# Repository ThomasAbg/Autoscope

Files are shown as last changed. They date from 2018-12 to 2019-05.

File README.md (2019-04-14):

# Autoscope - Latex template

## Dependencies

```
sudo apt-get install texlive-full python-pygments python-pip
sudo pip install pygments-style-monokailight
```

<br>

## Build

```
xelatex --shell-escape main.tex
```

<br>

## Provided commands

### Include code

Include a source code block :
```latex
\code{c}
void main(void){
    /*C code example*/
    }
\end{minted}
```

Include code in line :
```latex
\codeinline{text}{/*formatted text*/}
```

### Include figures

Set path to figures in `main.tex` :
```latex
\newcommand{\figures}{path/to/figures}
```

Include a figure :
```latex
\begin{figure}[H]
    \centering
    \includegraphics[width=0.3\linewidth]{\figures/image.png}
    \decoRule
    \caption[
    <Subtitle>]{
    <Subtitle>}
    \label{fig:<Subtitle>}
    \end{figure}
```

### Include equations

- `&` : Align columns
- `\\` : New ligne
- `^{}` : Superscript
- `_{}` : Subscript
- `\frac{}` : Fraction
- `\left(` & `\right)` : Scaled parenthesis
- `\left[` & `\right]` : Scaled braces

Example :
```latex
\begin{align*}
p(r,\theta,\varphi)&=G(\theta,\varphi)\cdot\left(\frac{P_{in}}{4\pi\cdot r^{2}}\right)&&(W/m^{2})\\
&=D(\theta,\varphi)\cdot\frac{P_{out}}{4\pi\cdot r^{2}}
\end{align*}
```

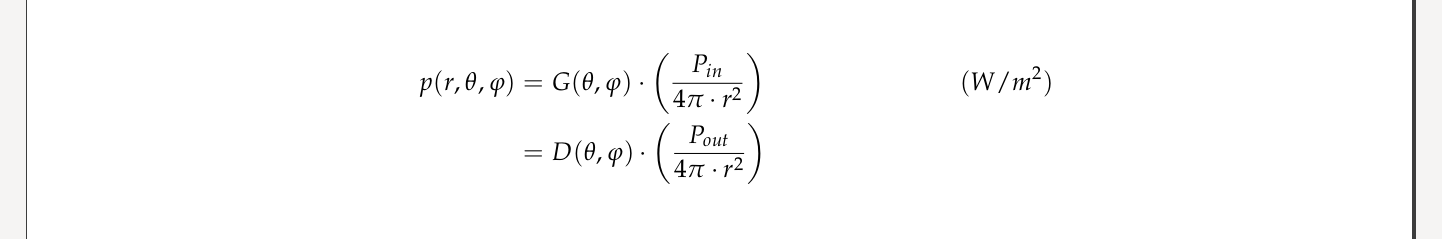
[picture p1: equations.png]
example_equations


### Include lists

Use `[label=$\bullet$]` for first level :
```latex
\begin{itemize}[label=$\bullet$]
	\item <item1>
	\item <item2>
	\item \begin{itemize}
		\item <item3.1>
		\item <item3.2>
		\end{itemize}
	\end{itemize}
```

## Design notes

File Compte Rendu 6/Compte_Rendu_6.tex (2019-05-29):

%.$ xelatex --shell-escape TP1.tex

%path to figures
\newcommand{\figures}{./Figures}

\documentclass[
11pt,
oneside,
french,
singlespacing,
liststotoc,
toctotoc,
headsepline,
]{MastersDoctoralThesis}

\usepackage{mathpazo}
\usepackage{fontspec}
\setmainfont[Ligatures=TeX, Mapping=tex-text]{TeX Gyre Pagella}
\setmonofont{FreeMonoBold}
\usepackage[backend=bibtex, style=authoryear, natbib=true]{biblatex}
\addbibresource{example.bib}
\usepackage[autostyle=true]{csquotes}
\usepackage{enumitem}
\usepackage{float}
\usepackage{amsmath}
\usepackage{minted}
\usepackage{xcolor}

\geometry{
	paper=a4paper,
	inner=2.5cm,
	outer=2.5cm,
	bindingoffset=0.5cm,
	top=1.5cm,
	bottom=1.5cm,
	}

\thesistitle{Autoscope\\Compte rendu final}
\supervisor {}
\examiner{}
\degree{\href{http://www.estei.fr/filiere/informatique-systemes-embarques}{MASTER Systèmes Embarqués}}
\author{Thomas ABGRALL\\Clément AILLOUD\\Thibaud LE DOLEDEC\\\href{https://www.github.com/thomaslepoix}{Thomas LEPOIX}}
\addresses{}
\subject{}
\keywords{}
\university{\href{http://www.estei.fr}{E.S.T.E.I.}}
\department{\href{http://www.estei.fr}{École Supérieure des Technologies Électronique, Informatique, et Infographie}}
\group{\href{http://www.estei.fr/filiere/informatique-systemes-embarques}{Département Systèmes Embarqués}}
\faculty{\href{http://www.estei.fr}{E.S.T.E.I.}}

\AtBeginDocument{
	\hypersetup{pdftitle=\ttitle}
	\hypersetup{pdfauthor=\authorname}
	\hypersetup{pdfkeywords=\keywordnames}
	}

\begin{document}

\mainmatter
\pagestyle{plain}
\usemintedstyle{monokailight}
%bash/Ruby/basemake/
\definecolor{gris}{gray}{0.97}
\definecolor{gris2}{HTML}{282828}
\definecolor{ubuntu}{HTML}{300A24}

\newcommand{\code}[1]{\begin{minted}[
linenos,
breaklines,
breakautoindent,
breakaftersymbolpost,
bgcolor=gris,
fontsize=\scriptsize,
obeytabs,
tabsize=4,
showtabs,
]{#1}}

\newcommand{\codeinline}[2]{\mintinline[fontsize=\footnotesize]{#1}{#2}}

%------------------------------------------------------------------

\begin{titlepage}
\begin{center}

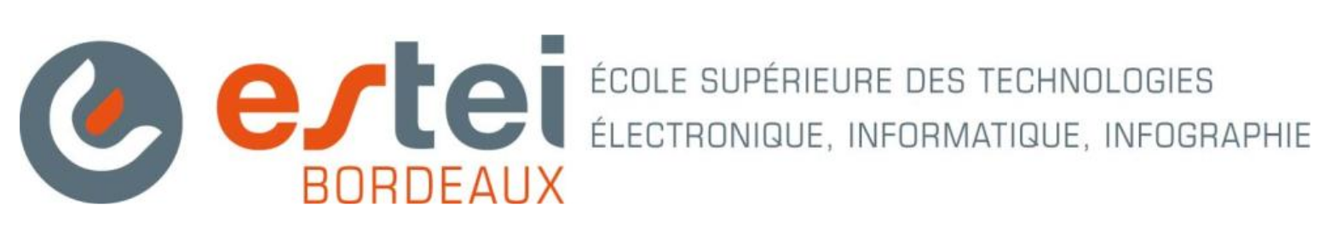
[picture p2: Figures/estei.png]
{\href{http://www.estei.fr}{}}
\vspace*{.06\textheight}
\vspace{1.5cm}\\
\textsc{\Large Projet de MASTER 2}\\[0.5cm]

\HRule \\[0.4cm]
{\huge \bfseries \ttitle\par}\vspace{0.4cm}
\HRule \\[1.5cm]

\large{\emph{Auteurs :}\\
\authorname}

\vspace{4cm}
\degreename\\[1cm]
{\vspace{0.4cm}\scshape\LARGE \univname}\\\deptname\\\groupname\\[1cm]

\vfill

{\large \today}\\[1cm]

\end{center}
\end{titlepage}

%------------------------------------------------------------------

%\begin{acknowledgements}
%\addchaptertocentry{\acknowledgementname} % Add the acknowledgements to the table of contents
%\end{acknowledgements}

\tableofcontents

\pagestyle{thesis}

%chapter Cahier des charges
%chapter Structure 3D
%chapter Hardware
%chapter Middleware
%chapter Software
%chapter Conclusion

\part{Partie de groupe}
\include{Chapters/Chapter1}
\include{Chapters/Chapter2}
\include{Chapters/Chapter3}
\include{Chapters/Chapter4}
\include{Chapters/Chapter5}
\include{Chapters/Chapter6}
\include{Chapters/Chapter7}
\part{Thomas LEPOIX}
%\include{Chapters/Lepoix/Chapter1}
\include{Chapters/Lepoix/Chapter2}
\include{Chapters/Lepoix/Chapter3}
\include{Chapters/Lepoix/Chapter4}
\include{Chapters/Lepoix/Chapter5}
\part{Thomas ABGRALL}
\include{Chapters/Abgrall/Chapter1}
\include{Chapters/Abgrall/Chapter2}
%\include{Chapters/Abgrall/Chapter3}
%\part{Clément AILLOUD}
%\include{Chapters/Ailloud/Chapter1}

\appendix

%\include{Appendices/AppendixA}

\end{document}

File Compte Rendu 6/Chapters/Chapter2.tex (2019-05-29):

\chapter{Optique}

\section{Explications sur le télescope de Dobson}

Le télescope est un instrument permettant d'observer le ciel en amplifiant la lumière captée des astres et en agrandissant l'image vue. Il réalise cela par un jeu de miroirs, à la différence de la lunette astronomique qui utilise un jeu de lentilles.

Il existe plusieurs types de télescope, celui de Newton est composé d'un miroir parabolique "primaire" concentrant la lumière vers un miroir plan "secondaire" la déviant vers l'oculaire, où l'utilisateur place son œil.

\begin{figure}[H]
    \centering
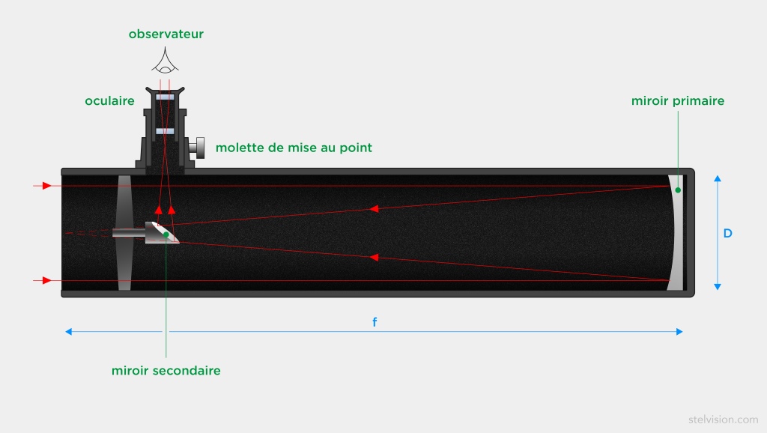
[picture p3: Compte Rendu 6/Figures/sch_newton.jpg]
    
    \decoRule
    \caption[
    Schéma du télescope de Newton\\(Schéma \textcopyright Stelvision)]{
    Schéma du télescope de Newton\\(Schéma \textcopyright Stelvision)}
    \label{fig:Schéma du télescope de Newton (Schéma copyright Stelvision)}
    \end{figure}

\vspace{1cm}

L'amplification lumineuse dépend du diamètre $D$ du miroir parabolique. Le grossissement dépend de la distance focale de la parabole $f$. Le diamètre détermine la luminosité et la finesse de l'image. La distance focale détermine le grossissement. Trop agrandir l'image par augmentation de la distance focale assombrit et dégrade sa qualité.

\vspace{1cm}

Le télescope de Dobson est un télescope de Newton doté d'une monture azimutale simplifiée. Il a été inventé par un astronome amateur et a les avantages d'être simple de fabrication et relativement peu onéreux pour un télescope.

\begin{figure}[H]
    \centering
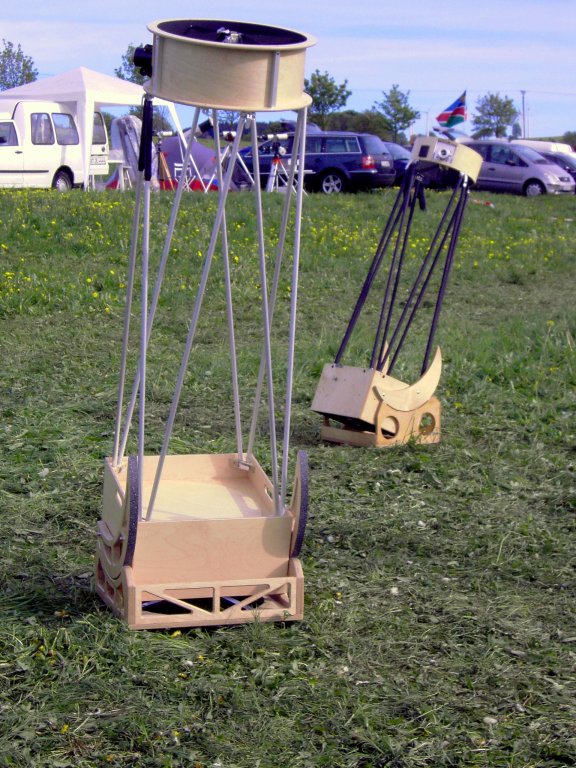
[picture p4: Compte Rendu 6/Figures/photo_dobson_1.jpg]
    
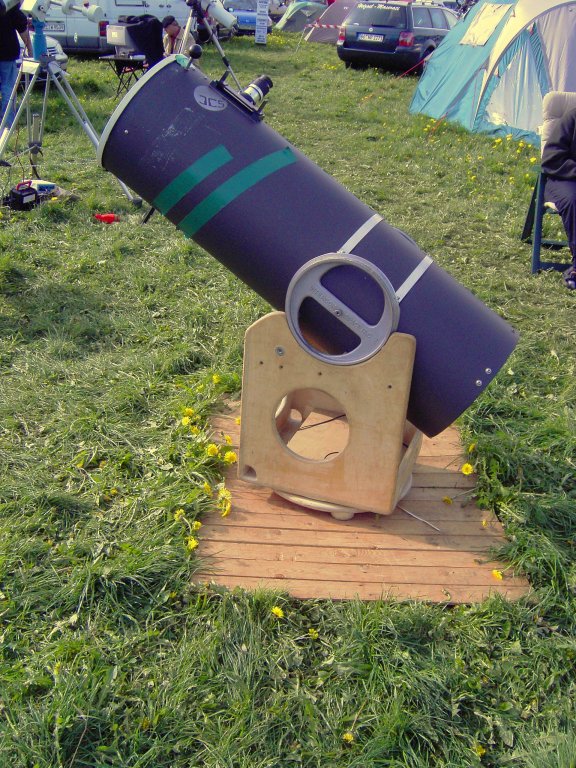
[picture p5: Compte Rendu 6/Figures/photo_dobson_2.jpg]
    
    \decoRule
    \caption[
    Télescopes de Dobson]{
    Télescopes de Dobson}
    \label{fig:Télescopes de Dobson}
    \end{figure}

\section{Choix de l'oculaire}

L'oculaire d'un télescope est un jeu de lentilles placé au plan focal de l'image produite par celui-ci. Il sert avant tout à faire de cette image présente au plan focal une image "à l'infini", c'est-à-dire nette sans accommodation de l'œil. Il permet également, par sa propre distance focale, d'ajuster le grossissement du télescope.

\begin{align*}
G&=\frac{f_{miroir primaire}}{f_{oculaire}}
\end{align*}

\vspace{1cm}

Un zoom est un objectif à lentilles mobiles et à distance focale variable. Il permet donc d'ajuster l'angle d'ouverture de l'appareil et de modifier son grossissement. Il existe des oculaires zoom pour télescope.

\vspace{1cm}

Le site internet Stelvision met à disposition un simulateur d'oculaires. Il permet, pour un télescope de caractéristiques $f$ et $D$ données, de visualiser l'image produite avec des oculaires de distances focales différentes. Quelques astres sont observables.

{\href{https://www.stelvision.com/simulateur-telescope/simulateur-telescope.php}{\codeinline{text}{https://www.stelvision.com/simulateur-telescope/simulateur-telescope.php}}}

\vspace{1cm}

Les caractéristiques de l'Autoscope sont les suivantes~:

\begin{align*}
D&=254mm&f&=1,27m
\end{align*}

\begin{figure}[H]
    \centering
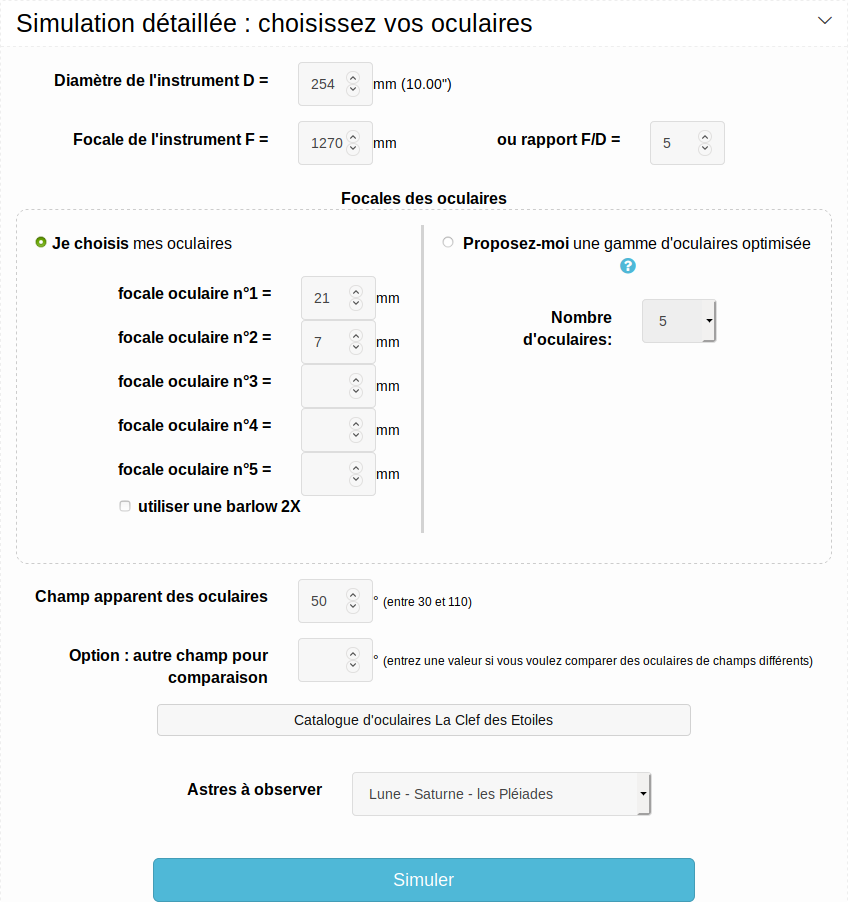
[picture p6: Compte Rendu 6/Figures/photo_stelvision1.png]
    
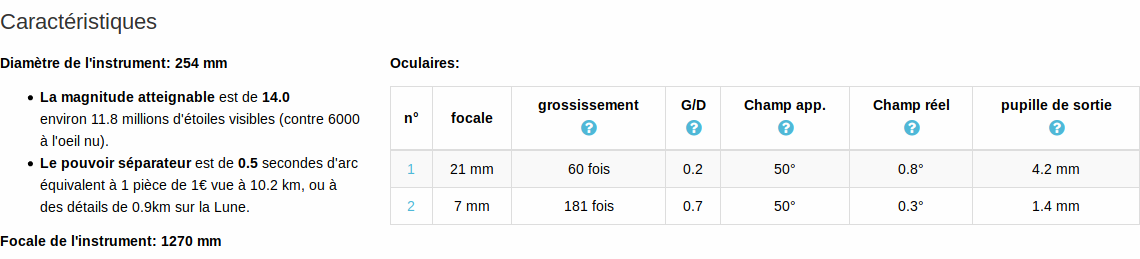
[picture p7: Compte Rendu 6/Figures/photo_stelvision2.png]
    
    \decoRule
    \caption[
	Simulateur de télescope Stelvision.com]{
    Simulateur de télescope Stelvision.com}
    \label{fig:Simulateur de télescope Stelvision.com}
    \end{figure}

\begin{figure}[H]
    \centering
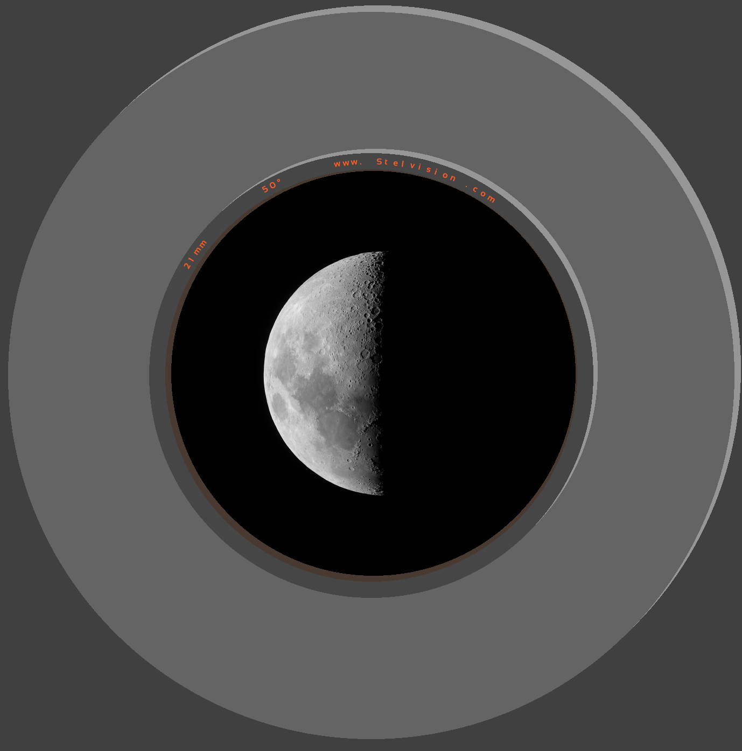
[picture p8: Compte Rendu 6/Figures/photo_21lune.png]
    
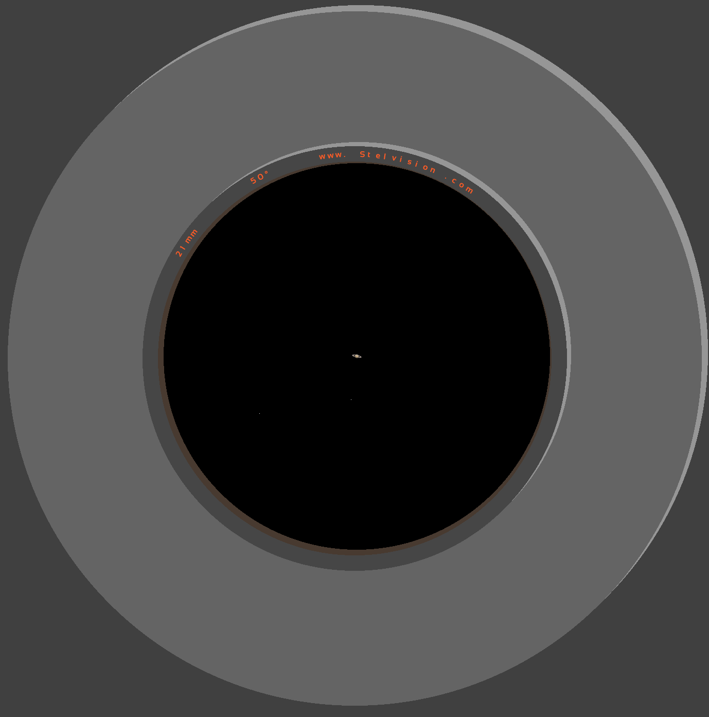
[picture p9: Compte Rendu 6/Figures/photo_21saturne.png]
    
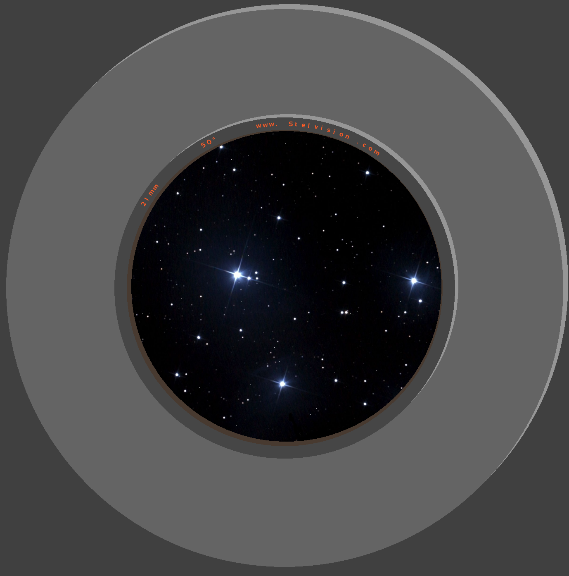
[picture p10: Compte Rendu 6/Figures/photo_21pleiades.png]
    
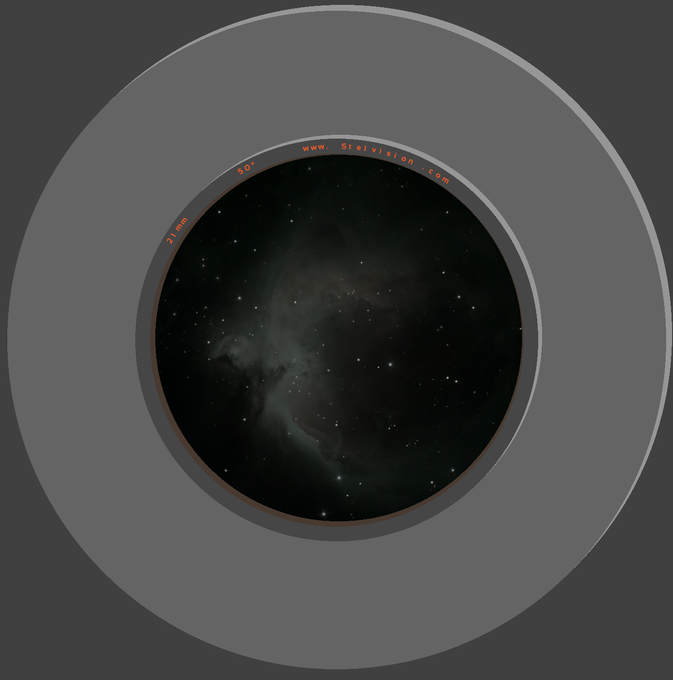
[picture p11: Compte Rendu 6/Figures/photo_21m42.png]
    
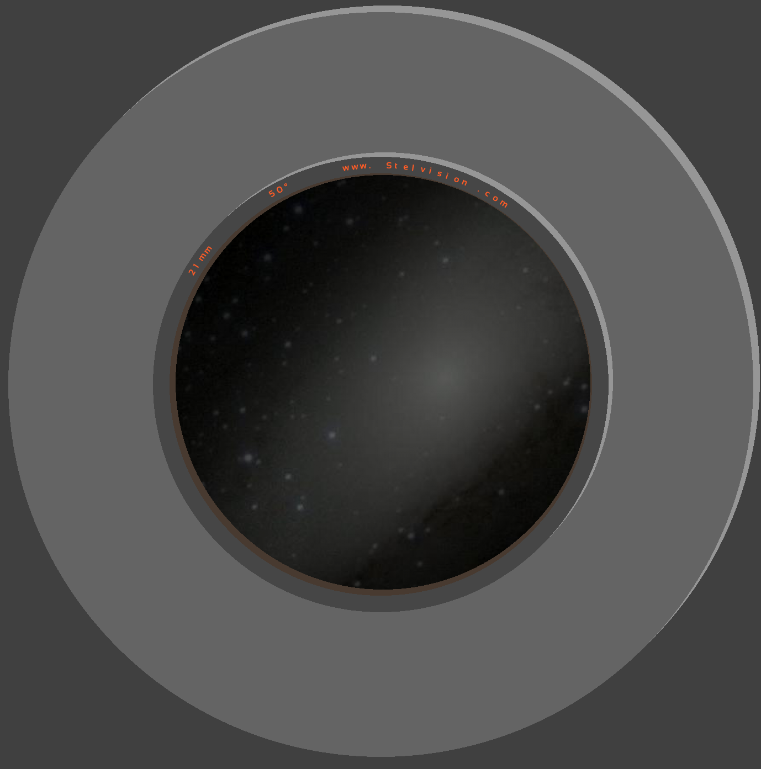
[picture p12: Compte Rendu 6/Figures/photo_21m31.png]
    
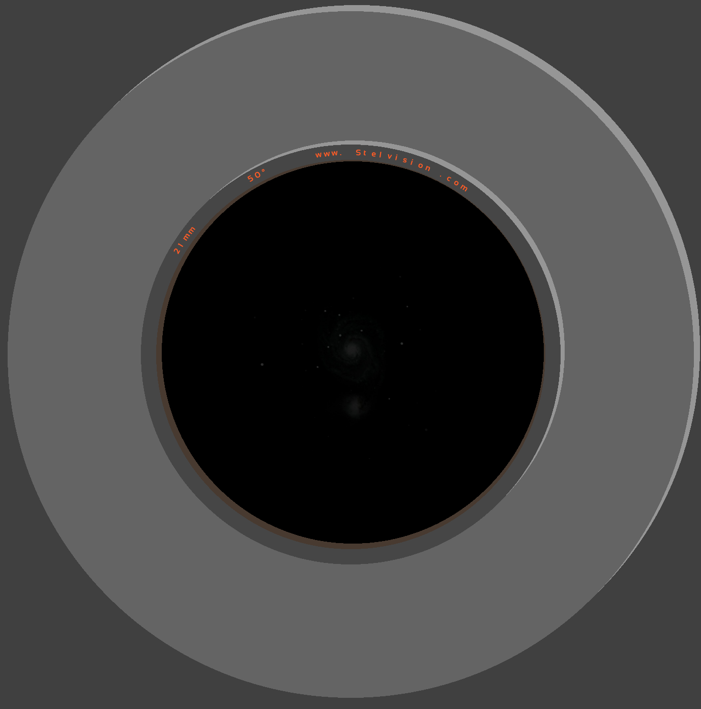
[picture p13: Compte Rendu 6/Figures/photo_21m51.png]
    
    \decoRule
    \caption[
	Résultats de simulation pour un oculaire de focale $f=21mm$\\Lune, Saturne, les Pléiades,\\galaxies M42, M31, M51]{
	Résultats de simulation pour un oculaire de focale $f=21mm$\\Lune, Saturne, les Pléiades,\\galaxies M42, M31, M51}
    \label{fig:	Résultats de simulation pour un oculaire de focale $f=21mm$ Lune, Saturne, les Pléiades, galaxies M42, M31, M51}
    \end{figure}

\begin{figure}[H]
    \centering
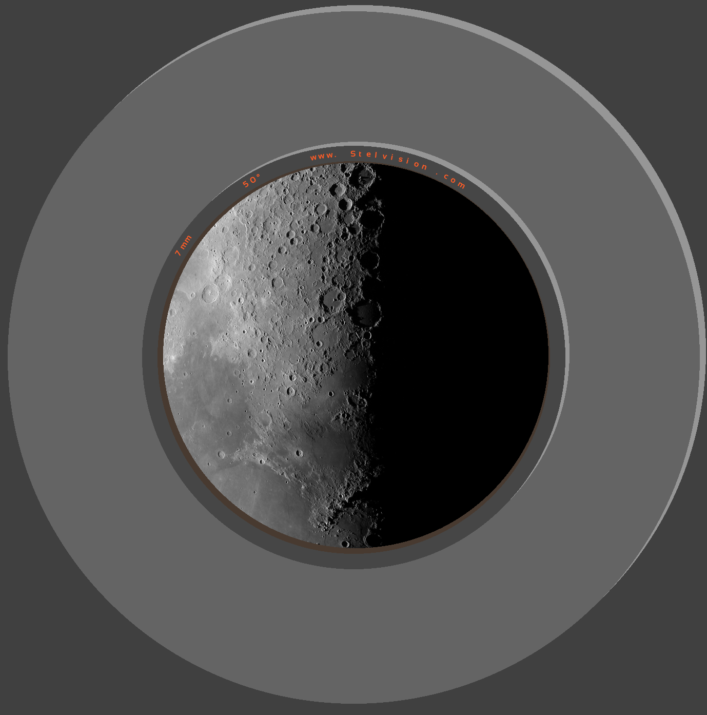
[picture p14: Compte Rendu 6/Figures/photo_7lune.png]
    
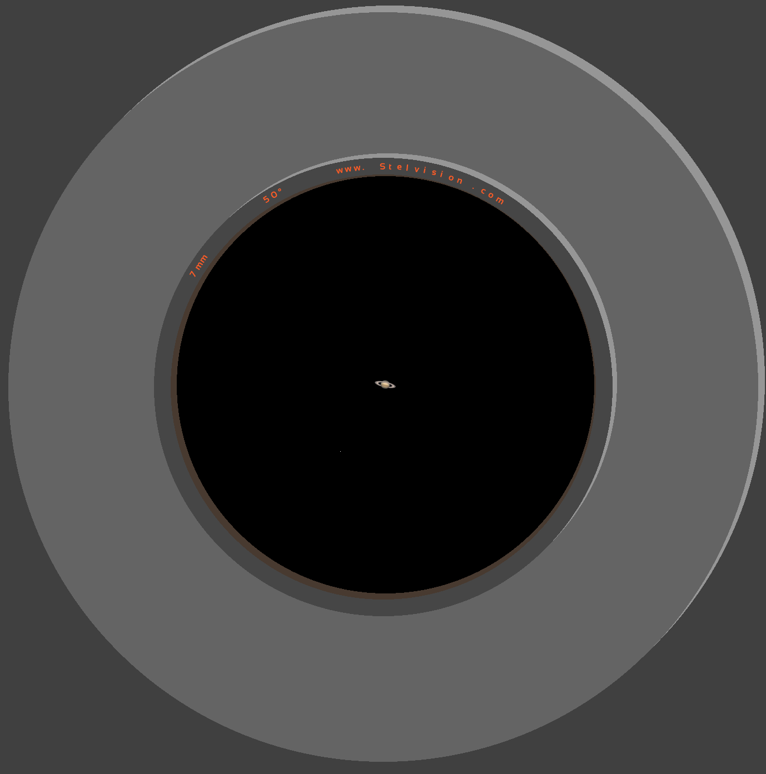
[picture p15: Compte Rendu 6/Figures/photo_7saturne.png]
    
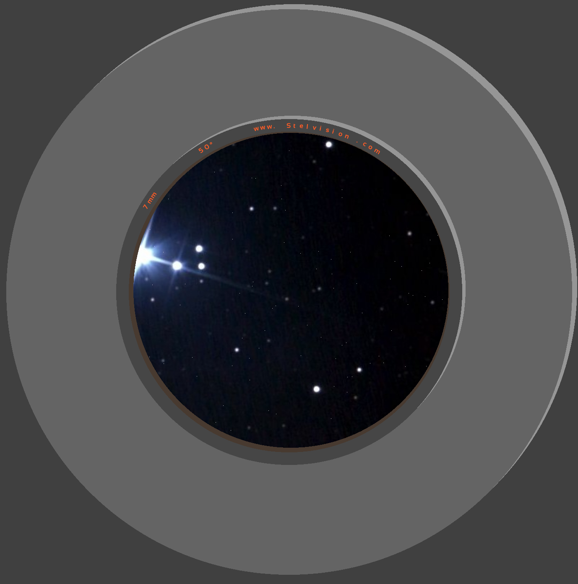
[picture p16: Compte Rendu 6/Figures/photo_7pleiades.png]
    
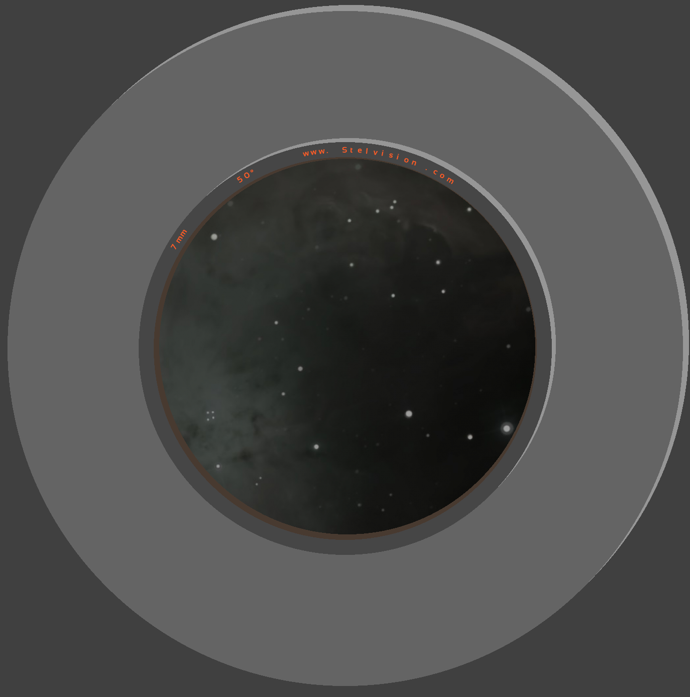
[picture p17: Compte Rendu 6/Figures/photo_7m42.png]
    
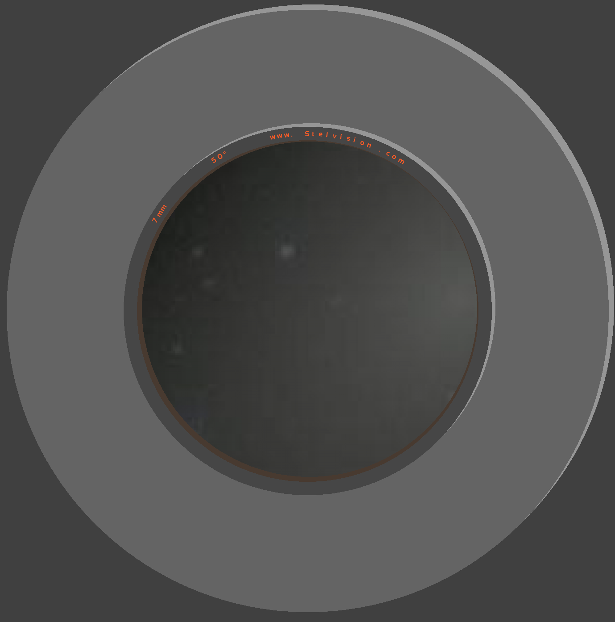
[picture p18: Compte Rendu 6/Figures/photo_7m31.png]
    
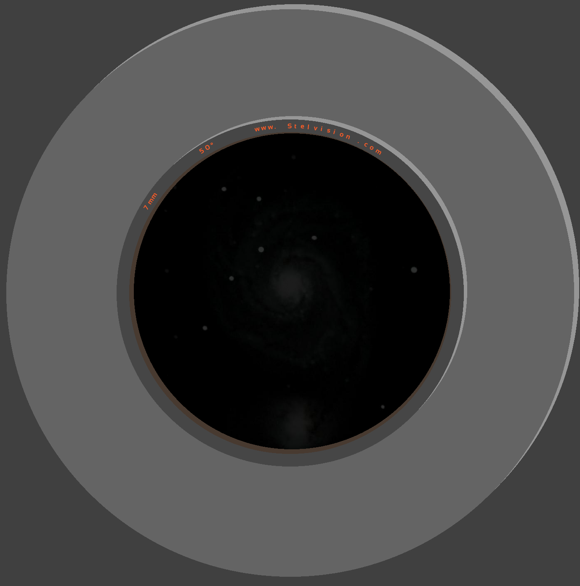
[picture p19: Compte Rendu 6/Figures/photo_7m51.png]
    
    \decoRule
    \caption[
	Résultats de simulation pour un oculaire de focale $f=7mm$\\Lune, Saturne, les Pléiades,\\galaxies M42, M31, M51]{
	Résultats de simulation pour un oculaire de focale $f=7mm$\\Lune, Saturne, les Pléiades,\\galaxies M42, M31, M51}
    \label{fig:	Résultats de simulation pour un oculaire de focale $f=7mm$ Lune, Saturne, les Pléiades, galaxies M42, M31, M51}
    \end{figure}

\vspace{1cm}

L'oculaire zoom choisi est polyvalent et permet un compromis satisfaisant entre grossissement et luminosité / vue d'ensemble.

{\href{https://www.astroshop.de/fr/oculaires/omegon-7-21mm-super-ploessl-oculaire-zoom-apo-1-25-/p,5084}{\codeinline{text}{https://www.astroshop.de/fr/oculaires/omegon-7-21mm-super-ploessl-oculaire-zoom}\\\codeinline{text}{-apo-1-25-/p,5084}}}

\begin{figure}[H]
    \centering
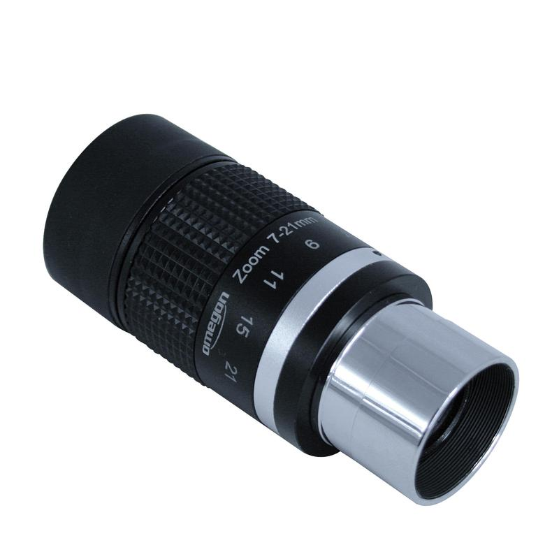
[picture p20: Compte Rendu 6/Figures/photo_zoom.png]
    
    \decoRule
    \caption[
    Oculaire zoom $21mm-7mm$]{
    Oculaire zoom $21mm-7mm$}
    \label{fig:Oculaire zoom $21mm-7mm$}
    \end{figure}

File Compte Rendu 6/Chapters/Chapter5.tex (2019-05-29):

\chapter{Organisation}

\section{Planning et répartition du travail}

En raison de l'abandon du projet par Thibaud LE DOLEDEC et Clément AILLOUD partis en stage, le projet ne pourra être mené à terme. Pour aborder la dernière ligne droite avant l'évaluation finale, un choix a donc été fait des tâches sur lesquelles travailler en priorité, au détriment d'autres qui demeureront inachevées.

\vspace{1cm}

Ci-dessous un diagramme représentant l’avancement des différentes tâches du projet. Le gris indique qu’une tâche est terminée ou à un niveau d’avancement satisfaisant et garantissant une maturité proche. Le orange indique les tâches en cours ou prioritaires au moment de l'évaluation finale. Les flèches représentent des liens de dépendance entre certaines tâches.

\begin{figure}[H]
    \centering
	
    \decoRule
    \caption[
    Diagramme de l'organisation temporelle du travail sur le projet]{
    Diagramme de l'organisation temporelle du travail sur le projet}
    \label{fig:Diagramme de l'organisation temporelle du travail sur le projet}
    \end{figure}

\section{Accessibilité du projet sur internet}

Le projet étant libre, il est disponible sur Github sous licence GPL-2. Nous tachons d'accompagner nos différents dépôts d'une documentation claire permettant d'obtenir les informations suivantes~:
\begin{itemize}[label=$\bullet$]
	\item Une description brève et précise sur le contenu du dépôt et son rôle au sein du projet.
	\item Une explication de la procédure à suivre pour utiliser le contenu du dépôt.
	\item Une explication de la procédure à suivre pour travailler sur le dépôt.
	\end{itemize}

\subsection{Dépôt principal}

{\href{https://github.com/thibaudledo/Autoscope}{\codeinline{text}{https://github.com/thibaudledo/Autoscope}}}

\vspace{1cm}

Le dépôt est organisé comme suit~:
\begin{itemize}[label=$\bullet$]
	\item Branche {\href{https://github.com/thibaudledo/Autoscope/tree/master}{\codeinline{text}{master}}}~: Sources du logiciel principal et explications sur le projet dans son ensemble.
	\item Release {\href{https://github.com/thibaudledo/Autoscope/releases}{\codeinline{text}{alpha}}}~: Paquets et fichiers binaires pour utiliser le projet "out of the box" (release expérimentale).
	\item Branche {\href{https://github.com/thibaudledo/Autoscope/tree/hardware}{\codeinline{text}{hardware}}}~: Fichiers Blender de la structure du télescope et fichiers KiCad de la carte électronique du projet.
	\item Branche {\href{https://github.com/thibaudledo/Autoscope/tree/doc}{\codeinline{text}{doc}}}~: Documentations et datasheets des composants et éléments utilisés pour le projet.
	\item Branche {\href{https://github.com/thibaudledo/Autoscope/tree/latex}{\codeinline{text}{latex}}}~: Fichiers LaTex et \codeinline{text}{.pdf} des comptes rendus sur le projet.
	\item Branche {\href{https://github.com/thibaudledo/Autoscope/tree/hello_mod}{\codeinline{text}{hello_mod}}}~: Sources d'un driver helloworld servant d'exemple.
	\item Branche {\href{https://github.com/thibaudledo/Autoscope/tree/a4988_mod}{\codeinline{text}{a4988_mod}}}~: Sources du driver des contrôleurs moteur et des capteurs de fin de course des moteurs.
	\item Branche {\href{https://github.com/thibaudledo/Autoscope/tree/mpu9250_mod}{\codeinline{text}{mpu9250_mod}}}~: Sources du driver de la centrale inertielle.
	\item Branche {\href{https://github.com/thibaudledo/Autoscope/tree/mtk3339d}{\codeinline{text}{mtk3339d}}}~: Sources du driver du GPS.
	\end{itemize}

\newpage
\subsection{Dépôt du système d'exploitation de la Raspberry-Pi}

{\href{https://github.com/thomaslepoix/meta-autoscope}{\codeinline{text}{https://github.com/thomaslepoix/meta-autoscope}}}

\vspace{1cm}

Il s'agit de la couche de métadonnées utilisées par Yocto pour construire le système d'exploitation Linux utilisé par la Raspberry-Pi du télescope. Une image pré-compilée du système d'exploitation figurera sur {\href{https://github.com/thibaudledo/Autoscope/releases}{la release \codeinline{text}{alpha} du dépôt principal}.

\vspace{1cm}

Le dépôt est organisé comme suit~:
\begin{itemize}[label=$\bullet$]
	\item Branche {\href{https://github.com/thomaslepoix/meta-autoscope/tree/rpi}{\codeinline{text}{rpi}}}~: Métadonnées Yocto et explications de comment compiler et installer le système d'exploitation.
	\item Branche {\href{https://github.com/thomaslepoix/meta-autoscope/tree/rpi-repo}{\codeinline{text}{rpi-repo}}}~: Données utilisées par Repo pour synchroniser le dépôt à d'autres dépôts de métadonnées Yocto utilisées pout construire l'OS.
	\end{itemize}

\subsection{Dépôt du plugin de Stellarium}

{\href{https://github.com/thibaudledo/Autoscope-Stellarium-plugin}{\codeinline{text}{https://github.com/thibaudledo/Autoscope-Stellarium-plugin}}}

\vspace{1cm}

Il s'agit du plugin de Stellarium contenant l'interface par laquelle l'utilisateur interagira avec le télescope. Un paquet pré-compilé pour linux de Stellarium incluant le plugin figure sur {\href{https://github.com/thibaudledo/Autoscope/releases}{la release \codeinline{text}{alpha} du dépôt principal}.

\vspace{1cm}

Le dépôt est organisé comme suit~:
\begin{itemize}[label=$\bullet$]
	\item Branche {\href{https://github.com/thibaudledo/Autoscope-Stellarium-plugin/tree/master}{\codeinline{text}{master}}}~: Sources du plugin, patch des sources de Stellarium et explications de comment compiler une version de Stellarium intégrant le plugin.
	\end{itemize}

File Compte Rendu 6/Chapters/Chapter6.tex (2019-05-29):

\chapter{Travail effectué par Thibaud LE DOLEDEC et Clément AILLOUD}

\section{Driver de la centrale inertielle (IMU)}

Clément AILLOUD a développé un driver Linux pour la centrale inertielle en utilisant le framework \codeinline{text}{iio}. Celui-ci supporte actuellement le gyroscope et l'accéléromètre mais pas le magnétomètre. Il est compatible avec les bus I2C et SPI. Sur l'Autoscope, le bus I2C sera utilisé.

Un patch du device tree permettant le support du driver est également fourni.

\vspace{1cm}

Le driver a été intégré au système d'exploitation du télescope. \codeinline{text}{iio} permet d'accéder aux données issues de l'IMU via le dossier suivant~:

\code{text}
root@autoscope ~ #
    ls /sys/bus/iio/devices/iio:device0/
        dev               in_accel_y_raw    in_anglvel_x_raw  in_temp_input  power
        in_accel_scale    in_accel_z_raw    in_anglvel_y_raw  name           subsystem
        in_accel_x_raw    in_anglvel_scale  in_anglvel_z_raw  of_node        uevent

    cat /sys/bus/iio/devices/iio:device0/name
        mpu9250-i2c
\end{minted}

\section{Interface utilisateur (Plugin de Stellarium)}

Le logiciel Stellarium offre la possibilité de développer des plugins aux fonctionnalités diverses. Nous avons décidé d'utiliser un plugin pour faire de Stellarium l'élément principal de l'interface utilisateur du télescope.

\vspace{1cm}

Thibaud LE DOLEDEC a développé un plugin de Stellarium permettant les actions suivantes~:
\begin{itemize}[label=$\bullet$]
	\item Rechercher un astre et le suivre tant à l'écran qu'avec le télescope (par l'envoi régulier de coordonnées spatiales à celui-ci).
	\item Demander au télescope ses coordonnées de position et de visée et afficher la vue du ciel simulé correspondante.
	\item Ordonner au télescope de prendre une photo. Il existe une interface destinée à configurer les paramètres de la caméra (temps d'exposition, etc.).
	\item Se connecter au serveur FTP du télescope pour récupérer les clichés du ciel.
	\item Afficher un aperçu de ce que voit le télescope à l'instant présent (retransmission d'un flux vidéo). Un espace actuellement matérialisé par un rectangle gris est destiné à cela.
	\end{itemize}

\vspace{1cm}

\begin{figure}[H]
    \centering
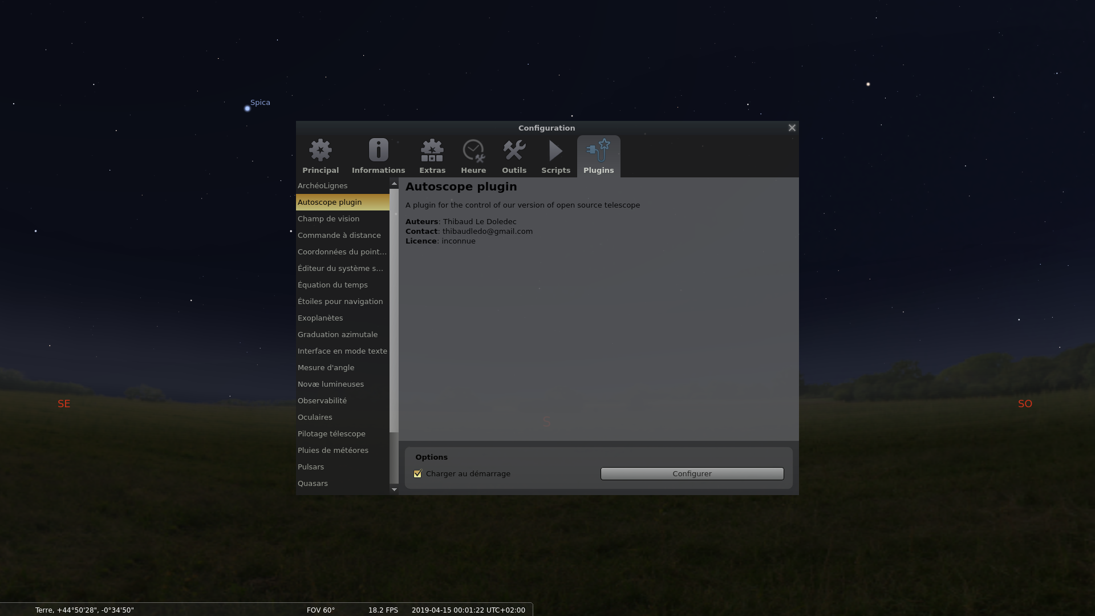
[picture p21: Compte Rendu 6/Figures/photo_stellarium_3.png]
    
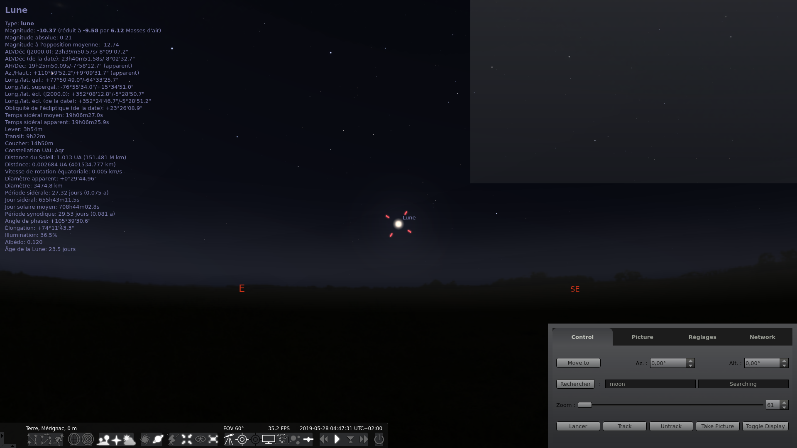
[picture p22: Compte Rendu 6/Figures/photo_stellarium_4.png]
    
    \decoRule
    \caption[
    Aperçu de l'interface du plugin de Stellarium]{
    Aperçu de l'interface du plugin de Stellarium}
    \label{fig:Aperçu de l'interface du plugin de Stellarium}
    \end{figure}

\vspace{1cm}

Le plugin fonctionne correctement, bien que certains éléments soient sûrement à retravailler lors du développement du logiciel principal du télescope.

La gestion de la communication FTP repose sur l'utilisation d'une librairie dépréciée \codeinline{text}{qtftp} qui a semblé poser problème lors des essais de déploiement du travail réalisé par Thibaud. L'idéal serait de se passer de cette librairie.

\vspace{1cm}

Thibaud et Clément ont rédigé un document disponible à l'adresse suivante qui explique la procédure à suivre pour développer un plugin de Stellarium.

{\href{https://github.com/thibaudledo/Autoscope/blob/latex/Tutoriel_Stellarium.pdf}{\codeinline{text}{https://github.com/thibaudledo/Autoscope/blob/latex/Tutoriel_Stellarium.pdf}}}

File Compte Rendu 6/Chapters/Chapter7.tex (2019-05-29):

\chapter{Travail restant à faire}

Ce chapitre existe dans le but de récapituler le travail restant à faire sur le projet de façon un minimum exhaustive.

\section{Structure du télescope}

La plupart des pièces du télescope vierge de toute modification a été imprimée, quelques parties assemblées. Le travail restant à faire est conséquent et consiste en la modification du design du télescope en vue d'y intégrer~:
\begin{itemize}[label=$\bullet$]
	\item La carte électronique et la Raspberry-pi, face vers le sol, sous le miroir primaire.
	\item Les modules GPS et IMU, placés le long de la structure du télescope. L'interprétation des données émises par l'IMU dépendra de son positionnement.
	\item Les moteurs d'azimut et d'élévation ainsi que leurs courroies et tringles. Les roues crantées à fixer sur l'axe des moteurs n'ont pas été choisies. Leur diamètre reste à déterminer.
	\item Les boutons poussoirs, capteurs de fin de course des mouvements engendrés par les moteur. Leur position devra être déterminée avec précision.
	\item Tout le dispositif maintenant l'oculaire, le moteur permettant de l'actionner, les capteurs de fin de course associés (le mouvement de l'oculaire s'étend sur environ un quart de tour), ainsi que le module caméra. Ce dispositif devra être conçu avec le plus grand soin et la plus grande attention afin de permettre un réglage fin du télescope et d'obtenir une image nette. Il est conseillé de se renseigner la procédure de $collimation$ des télescopes avant de se lancer dans la conception.
	\end{itemize}

\section{Hardware}

Il reste uniquement à faire la connectique des éléments déportés de la carte électronique.

Un ventilateur de refroidissement du miroir peut aussi être choisi, nous ne nous sommes pas renseignés sur l'utilité avérée ou non de cet élément.

\section{Système d'exploitation}

\begin{itemize}[label=$\bullet$]
	\item Sécurisation du système par la mise en place d'un pare feu avec \codeinline{text}{iptables} (et donc l'étude des ports utilisés, ainsi que le choix d'un port ne posant aucun conflit pour le transfert vidéo et la communication avec le plugin Stellarium), une gestion plus fine des droits de chaque utilisateur Linux, etc. L'abandon de FTP au profit de SFTP comme protocole de transfert d'images serait souhaitable (\codeinline{text}{openSSH} déjà utilisé comme serveur SSH permet cela).
	\item La mise en place d'un système de mise à jour de l'OS. \codeinline{text}{SWUpdate} semble être une solution plus intéressante que \codeinline{text}{Mender} puisque nettement plus souple et configurable, tant dans la façon de mettre à jour le système que dans la façon de déclencher la mise à jour. Dans tous les cas, ces systèmes de mise à jour nécessitent d'utiliser un bootloader en plus du firmware du GPU de la Raspberry-Pi, or l'overlay du device tree \codeinline{text}{pi3-disable-bt} (nécessaire pour la communication avec le GPS) semble être incompatible avec U-Boot. Une tentative de transformer l'overlay en patch n'a pas résolu le problème, les investigations n'ont pas été poussées davantage.
	\item L'optimisation de l'OS. Plusieurs choses peuvent être optimisées, la mémoire occupée, le temps de boot (qui peut être optimisé à plusieurs niveau, les plus faciles à travailler étant le niveau applicatif et le niveau de processus d'initialisation, ensuite viennent Linux et bootloader). Sur Yocto, le fichier \codeinline{text}{meta-autoscope/conf/distro/autoscope.conf} permet de se délester du support d'éléments inutilisés. Le lien suivant est une documentation intéressante~:\\{\href{https://embexus.com/2017/05/16/embedded-linux-fast-boot-techniques/}{\codeinline{text}{https://embexus.com/2017/05/16/embedded-linux-fast-boot-techniques/}}}
	\end{itemize}

\section{Support de la caméra}

Il faut évaluer les possibilités de paramétrage de la capture photo que permettent les logiciels \codeinline{text}{raspistill}, \codeinline{text}{raspiyuv}, etc. Peut être cela est suffisant, peut être existe il une librairie de plus bas niveau utilisable dans un programme C/C++, peut être sera il nécessaire d'en développer une. Il semble peu probable qu'il faille modifier le driver de la caméra.

\section{Transfert du flux vidéo sur le réseau}

La communauté Raspberry-Pi fournit une librairie Python de contrôle de la caméra, il semble qu'elle permette un transfert sur le réseau du flux vidéo sans latence excessive. La recette Yocto pour intégrer ladite librairie a été écrite mais pas celle permettant l'ajout de toutes celles qu'elle même utilise.

Il serait préférable de trouver une librairie équivalente en C/C++, ou à défaut de l'écrire.

\vspace{1cm}

Il n'a pas été déterminé s'il est plus pertinent d'intégrer le logiciel de transmission du flux vidéo au logiciel principal du télescope ou s'il est plus pertinent d'en faire un autre logiciel.

Le serveur vidéo devra probablement s'interrompre le temps que le télescope utilise la caméra pour prendre une photo ponctuelle. Dans le cas où il serait un logiciel distinct du logiciel principal, les signaux seraient sûrement pour ce dernier un moyen de contrôle suffisant. Par exemple \codeinline{text}{SIGSTOP} et \codeinline{text}{SIGCONT} s'il suffit de mettre le serveur en pause, \codeinline{text}{SIGUSR1} et \codeinline{text}{SIGUSR2} si le serveur doit effectuer des actions de connexion/déconnexion au client ainsi qu'à la caméra.

\section{Daemon du GPS}

Le daemon du GPS n'a pas été testé dans un environnement où la connexion est suffisamment bonne pour que le GPS parvienne à calculer sa position géographique. Il suffit probablement de l'emmener à l'extérieur. Ce test permettrait de valider définitivement le fonctionnement du daemon ainsi que du GPS.

Une meilleure gestion des cas d'erreurs dans le code du daemon serait la bienvenue.

\section{Driver des contrôleurs moteur}

Le cœur du driver des contrôleurs moteur fonctionne. L'organe de communication avec le logiciel principal du télescope est le dernier à être en cours de développement bien que proche d'un état satisfaisant.

Quelques éléments légers resteront a modifier. Une phase de refactoring du code sera également nécessaire.

\section{Driver de la centrale inertielle (IMU)}

\begin{itemize}[label=$\bullet$]
	\item Le plus important du travail a été réalisé puisque le driver existe et supporte le gyroscope et l'accéléromètre de la centrale inertielle. Il reste à programmer le support du magnétomètre.
	\item Davantage de documentation sur le fonctionnement du driver serait également bienvenue.
	\item Enfin, une série de tests reste à concevoir et à mettre en œuvre pour valider le fonctionnement du driver.
	\end{itemize}

\section{Plugin de Stellarium}

\begin{itemize}[label=$\bullet$]
	\item La librairie FTP utilisée \codeinline{text}{qftp} pose problème et est dépréciée, il faudrait se passer de son utilisation. Il serait judicieux d'en profiter pour migrer vers SFTP, plus sécurisé.
	\item Une partie du code sera probablement à retravailler conjointement au développement du logiciel principal du télescope, ainsi que du serveur vidéo.
	\end{itemize}

\section{Logiciel principal du télescope (Autoscope-core)}

\begin{itemize}[label=$\bullet$]
	\item Intégration dans un programme unique des fragments d'interface avec les différents organes logiciels du télescope (drivers moteurs et IMU, daemon GPS, plugin Stellarium, etc). Ces fragments se trouvent sur la branche {\href{https://github.com/thibaudledo/Autoscope/tree/master}{\codeinline{text}{master} du dépôt git principal}} et sont voués à disparaître une fois cette tâche effectuée.
	\item Développement de l'algorithme de déplacement du télescope. Celui-ci va dépendre des données qu'il est possible d'obtenir de la centrale inertielle, des possibilités du driver des contrôleurs moteur, ainsi que de la structure du télescope et la façon dont sera intégrée le hardware.
	\end{itemize}

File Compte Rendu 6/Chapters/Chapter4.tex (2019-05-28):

\chapter{Architecture}

\section{Architecture système}

\begin{figure}[H]
    \centering
    
    \decoRule
    \caption[
    Schéma fonctionnel du télescope]{
    Schéma fonctionnel du télescope}
    \label{fig:Schéma fonctionnel du télescope}
    \end{figure}

\vspace{1cm}

Le télescope sera composé d'une carte Raspberry Pi à laquelle sera connecté une carte de même format accueillant le module GPS, le module IMU (centrale inertielle), les contrôleurs des moteurs ainsi que l'alimentation du système. Les modules GPS et IMU seront probablement déportés afin de les éloigner des moteurs et de leurs perturbations électromagnétiques.

La caméra et l'éventuel écran tactile seront directement connectés à la Raspberry Pi.

Trois moteurs permettront de mouvoir le télescope~:
\begin{itemize}[label=$\bullet$]
	\item Un pour l'azimut.
	\item Un pour l'élévation.
	\item Un pour le zoom.
	\end{itemize}

\vspace{1cm}

Pour interagir avec le télescope, l'utilisateur aura le choix d'utiliser l'éventuel écran tactile embarqué ou bien un ordinateur connecté au télescope via le réseau. Cette solution étant la voie d'accès préférentielle aux contrôles du télescope.

\section{Architecture logicielle}

%TODO camera
\begin{figure}[H]
    \centering
    
    \decoRule
    \caption[
    Architecture logicielle du télescope]{
    Architecture logicielle du télescope}
    \label{fig:Architecture logicielle du télescope}
    \end{figure}

\vspace{1cm}

Le fonctionnement du télescope reposera sur plusieurs briques logicielles.
\begin{itemize}[label=$\bullet$]
	\item Au plus bas niveau les drivers permettant de recueillir les données que fournissent l'IMU et le GPS, ainsi que d'actionner les moteurs, ceux-ci étant asservis par des capteurs de positions extrêmes.
	\item À l'étage suivant le logiciel principal du télescope permettant de connaître les coordonnées précises du télescope (position géographique, orientation spatiale) et d'ordonner au télescope d'adopter une orientation particulière.
	\item À l'étage supérieur l'interface utilisateur permettant de prendre des clichés du ciel, d'orienter le télescope selon Stellarium, de placer Stellarium selon l'orientation du télescope, mais avant tout de basculer entre les différents modes du télescope~:
	\begin{itemize}
		\item Observation du ciel via la caméra.
		\item Exploration virtuelle du ciel avec Stellarium (local ou distant).
		\item Amélioration d'images avec Siril.
		\item Interaction avec le système d'exploitation du télescope.
		\end{itemize}
	\end{itemize}

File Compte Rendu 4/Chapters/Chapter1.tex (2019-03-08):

\chapter{Avancement général}

Nous avons commencé à monter le télescope. Le socle circulaire, les deux croissants ainsi que le support du miroir secondaire.

\vspace{1cm}

Plusieurs parties indépendantes seront bientôt terminées et le projet approche une phase d'intégration.

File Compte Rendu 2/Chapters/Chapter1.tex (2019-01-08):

\chapter{Évolution du cahier des charges}
\label{chapter1}

Plusieurs éléments du cahier des charges ont été amenés à changer depuis la première revue de projet.

\section{Nécessité du traçage d'astre}

Le traçage d'astre, vu au départ comme une fonctionnalité intéressante, s'est imposé comme une fonctionnalité nécessaire. En effet il peut être particulièrement difficile pour une personne non initiée à l'astronomie de positionner le télescope vers un astre précis ou de reconnaître un astre que l'on observe. Il nous est donc apparu primordial que le télescope permette d'affranchir l'utilisateur de la nécessité d'avoir des bases en astronomie pour observer le ciel.

\vspace{1cm}

En étudiant les solutions disponibles nous avons trouvé des logiciels de simulation du ciel, comme par exemple le logiciel libre Stellarium.

\begin{figure}[H]
    \centering
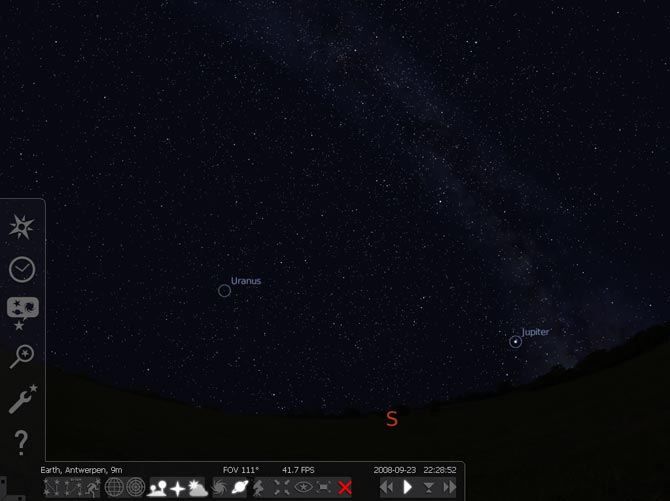
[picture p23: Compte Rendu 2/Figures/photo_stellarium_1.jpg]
    
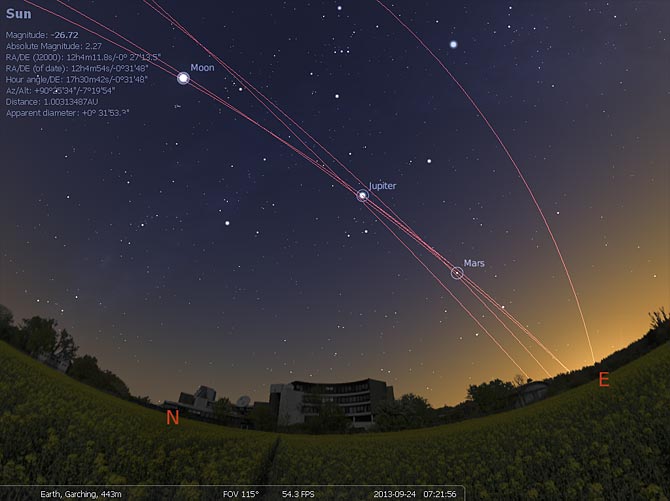
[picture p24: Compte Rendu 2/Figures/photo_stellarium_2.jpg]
	
    \decoRule
    \caption[
    Captures d'écran de Stellarium]{
    Captures d'écran de Stellarium}
    \label{fig:Captures d'écran de Stellarium}
    \end{figure}

\vspace{1cm}

Celui-ci permet notamment~:
\begin{itemize}[label=$\bullet$]
	\item De connaître les coordonnées d'un astre par rapport à l'endroit sur terre où se situe l'observateur.
	\item De s'orienter dans le ciel selon des coordonnées.
	\item De s'interfacer avec d'autres systèmes logiciels et/ou matériels
	\end{itemize}

Nous avons donc décidé dans un premier temps de développer une interface pour piloter le télescope depuis un ordinateur distant doté de Stellarium. Puis éventuellement d'embarquer Stellarium dans l'ordinateur du télescope. Ainsi Stellarium fera partie intégrante de son interface utilisateur.

Celle-ci pourrait être alors un menu discret permettant de passer de l'exploration virtuelle du ciel à la vue correspondante à travers le télescope à d'autres élément comme un dispositif d'amélioration de la qualité des images prises.

\section{Nécessité d'une centrale inertielle et d'un GPS}

L'utilisation d'un logiciel de traçage d'astre tel Stellarium nécessite la compatibilité du télescope avec les coordonnées d'azimut et d'élévation couramment utilisées en astronomie. Il est également nécessaire pour cela de savoir de quel endroit sur terre le télescope observe le ciel, d'où l'utilisation d'un GPS.

\vspace{1cm}

Pour connaître l'azimut et l'élévation, il faut avoir des repère dans les deux dimensions. Un magnétomètre permet de déterminer la direction du nord et un accéléromètre permet de connaître la direction du sol, c'est à dire la verticale.

Une centrale inertielle est un composant intégrant un magnétomètre, un accéléromètre et un gyroscope. Elle permet de connaître directement les coordonnées absolues de son orientation dans l'espace.

\section{Changement de SoC}

L'utilisation de Stellarium requiert au minimum $512MiB$ de RAM et $1GiB$ pour une utilisation optimale. Or la carte PICO-PI ne dispose que de $512MiB$ de RAM, elle est donc incapable de faire fonctionner Stellarium correctement.

\vspace{1cm}

Nous avons choisi une Raspberry Pi 3 B avec $2GiB$ de RAM en remplacement. En dépit de ses faibles capacités d'industrialisations, la Raspberry Pi a l'avantage d'être populaire dans le milieu de l'électronique amateur, c'est-à-dire le publique le plus susceptible d'être intéressé par ce genre de projet.

\begin{figure}[H]
    \centering
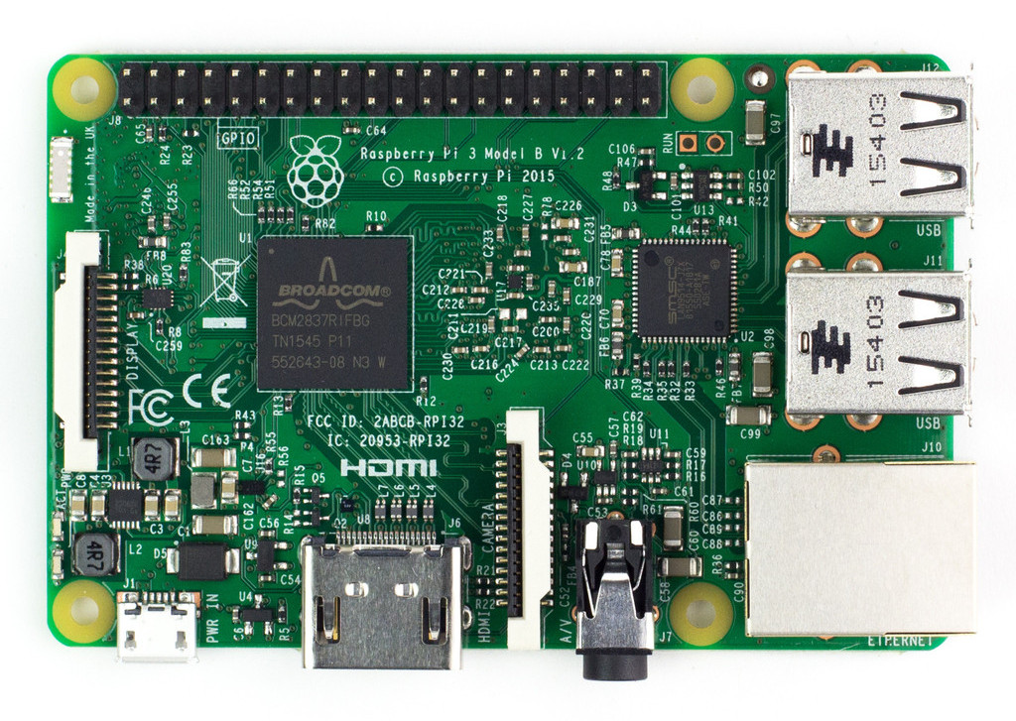
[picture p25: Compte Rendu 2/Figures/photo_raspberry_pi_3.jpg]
    
    \decoRule
    \caption[
    Captures d'écran de Stellarium]{
    Captures d'écran de Stellarium}
    \label{fig:Captures d'écran de Stellarium}
    \end{figure}

\vspace{1cm}

La caméra et l'écran utilisés ne seront donc plus ceux fournis avec la PICO-PI mais ceux de la Raspberry Pi, à savoir~:
\begin{itemize}[label=$\bullet$]
	\item Le module Raspicam v2.1 intégrant une caméra IMX219 de $8Mpx$.
	\end{itemize}

\vspace{1cm}

L'écran demeure toutefois une option, celui-ci sera intégré si le télescope embarque Stellarium.

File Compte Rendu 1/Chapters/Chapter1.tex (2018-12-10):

\chapter{Cahier des charges}
\label{chapter1}

%Introduction
%Spécifications techniques
%	en résumé
%Organisation > répartition, trello, github, slack
%étude de solutions techniques

%part Cahier des charges
%part Structure 3D
%part Hardware
%part Middleware
%part Software
%part Conclusion

\section{Introduction}

Le but de ce projet est de réaliser un télescope électronique. C'est-à-dire un télescope doté d'une caméra et dont les mouvements sont pilotables via une interface homme-machine.

\vspace{1cm}

Ce projet se base sur un projet existant~: un télescope de type Newton conçu pour être imprimable à l'imprimante 3D.

Lien du projet~: \url{https://blog.dagoma.fr/telescope-imprime-en-3d/}

\begin{figure}[H]
	\centering
    
    \decoRule
    \caption[
    Photo du télescope imprimé]{
    Photo du télescope imprimé}
    \label{fig:Photo du télescope imprimé}
	\end{figure}

\section{Spécifications techniques}

Certaines fonctionnalités devront impérativement être implémentées pour que le télescope soit validé. D'autres sont envisagées et seront implémentées dans la mesure du possible avant l'évaluation de ce projet. Certaines le seront éventuellement passé cette date, d'autres ne le seront peut être jamais.

De plus nous nous imposons dès le départ l'utilisations de certains matériels.

\subsection{Fonctionnalités obligatoires}

Le télescope devra être capable d'effectuer des mouvements d'azimut à 360\textdegree et des mouvements d'élévation dont l'amplitude dépend de la structure du télescope utilisé comme point de départ.

\vspace{1cm}

Il disposera d'une caméra permettant de prendre des clichés.

\vspace{1cm}

Concernant l'interface homme-machine, il disposera d'une interface réseau rudimentaire ainsi que d'un écran tactile. Il sera donc doté d'un logiciel de pilotage.

\subsection{Fonctionnalités envisagées}

Le pilotage du télescope via une interface web est sérieusement envisagé.

\vspace{1cm}

D'autres fonctionnalités logicielles plus évoluées telles qu'un dispositif d'amélioration de la qualité des images ou un logiciel de traçage / reconnaissance d'astre seront étudiées.

Idéalement ces solutions seront embarquées dans le télescope, toutefois la possibilité de les déporter vers un serveur distant d'une plus grande puissance de calcul n'est pas exclue.

Ces fonctionnalités étant estimées d'une complexité importante, il est probable que leur développement demande beaucoup de temps et qu'elles ne soient pas terminées à la fin du projet.

\vspace{1cm}

L'ajout d'une batterie permettant l'autonomie du télescope est également envisagé mais n'est pas vu comme une priorité.

\subsection{Matériel}

Nous avons choisi d'utiliser comme élément central un SoC (System on Chip) industrialisable, ce qui exclut l'usage des cartes Raspberry Pi par exemple. Nous avons retenu la carte PICO-PI-IMX7D de NXP.

Cette carte est composé d'un module PICO-IMX7D équipé d'un processeur IMX7D et d'une carte d'interface format Raspberry Pi.

\begin{figure}[H]
	\centering
    
	\hspace{1cm}
    
    \decoRule
    \caption[
    Module PICO-IMX7D à droite et carte PICO-PI à gauche]{
    Module PICO-IMX7D à droite et carte PICO-PI à gauche}
    \label{fig:Module PICO-IMX7D à droite et carte PICO-PI à gauche}
	\end{figure}
 
\vspace{1cm}

La caméra et l'écran choisis font partie du "Starter kit" commercialisé avec la carte et sont de références respectives Omnivision ov5645 et Chimei Innolux EJ050NA-01G.

La caméra pourra éventuellement être remplacée par une caméra plus performante si le besoin s'en fait ressentir.

\subsection{Résumé des exigences}

\begin{figure}[H]
	\centering
    
    \decoRule
    \caption[
    Tableau récapitulatif des exigences du projet]{
    Tableau récapitulatif des exigences du projet}
    \label{fig:Tableau récapitulatif des exigences du projet}
	\end{figure}

\section{Organisation}

%outils
%répartition du travail

En tant que groupe de quatre personne, nous avons choisi de travailler en appliquant les méthodes agiles. Ainsi la répartition du travail au sein du groupe se fera de façon dynamique en fonction des aptitudes de chacun et de la charge de travail nécessaire pour terminer une tache donnée en un temps imparti.

\vspace{1cm}

Nous avons sélectionné quelques outils pour travailler de façon optimale~:
\begin{itemize}[label=$\bullet$]
	\item {\href{https://slack.com}{Slack}} comme moyen de communication.
	\item {\href{https://trello.com}{Trello}} comme outil de gestion de projet.
	\item {\href{https://github.com}{Github}} comme hébergeur de code source.
	\begin{itemize}
		\item Dépôt dédié à la layer Yocto du système d'exploitation de la PICO-PI~:\\\url{https://github.com/thomaslepoix/meta-autoscope}
		\item Dépôt dédié aux autres éléments du projet~:\\\url{https://github.com/thibaudledo/Autoscope}
		\end{itemize}
	\end{itemize}

\vspace{1cm}

À l'issue d'une étude technique préliminaire, nous avons dressé un schéma fonctionnel provisoire du système.

\begin{figure}[H]
	\centering
    
    \decoRule
    \caption[
    Schéma fonctionnel provisoire du système électronique du télescope]{
    Schéma fonctionnel provisoire du système électronique\\du télescope}
    \label{fig:Schéma fonctionnel provisoire du système électronique du télescope}
	\end{figure}

\vspace{1cm}

Nous avons donc pu trier et organiser les différentes tâches à accomplir et en prioriser certaines représentées en orange sur le diagramme ci-dessous. Les tâches encadrées de gras sont celles jugées les plus critiques pour l'accomplissement du projet.

\begin{figure}[H]
	\centering
    
    \decoRule
    \caption[
    Diagramme de l'organisation temporelle du travail sur le projet]{
    Diagramme de l'organisation temporelle du travail sur le projet}
    \label{fig:Diagramme de l'organisation temporelle du travail sur le projet}
	\end{figure}

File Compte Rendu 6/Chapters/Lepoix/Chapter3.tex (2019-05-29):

\chapter{Système d'exploitation}

\section{Introduction}

L'avantage d'utiliser une carte Raspberry-Pi pour automatiser le télescope est la possibilité de disposer d'un système d'exploitation, en particulier d'une distribution GNU/Linux.

\vspace{1cm}

Yocto est un outil qui permet de créer ses propres distributions. Son utilisation permet d'obtenir un système d'exploitation adapté à l'application à laquelle il se destine sans éléments superflus consommant inutilement de la mémoire, de la puissance de calcul ou du temps de réaction. Il facilite de plus la reproductibilité du système.

Yocto est un outils complexe dont il est difficile d'avoir une vue d'ensemble. Ce chapitre n'en expliquera pas le fonctionnement, en revanche pour permettre de comprendre et de se réapproprier le travail effectué, tous les éléments de code permettant de mettre en place des fonctionnalités seront détaillés.

Pour plus d'informations, le fonctionnement global de Yocto est décrit dans un précédent rapport de projet~: {\href{https://github.com/thomaslepoix/ESTEI/blob/master/M1_Projet_Telecommande_Raspberry-Pi/Hardware_Middleware.pdf}{\codeinline{text}{https://github.com/thomaslepoix/ESTEI/blob/master/M1_Projet_Teleco}\\\codeinline{text}{mmande_Raspberry-Pi/Hardware_Middleware.pdf}}}

\vspace{1cm}

Le travail sur le système d'exploitation de la Raspberry-Pi du télescope s'articule autour des points suivants~:
\begin{itemize}[label=$\bullet$]
	\item Mettre en place une configuration réseau permettant un accès simple au télescope depuis un ordinateur, via Wifi notamment.
	\item Configurer le noyau Linux de sorte que toutes les briques logicielles soient capables de fonctionner. Cela passe notamment par une configuration du device tree.
	\item Intégrer les différentes briques logicielles et assurer la coordination de leurs fonctionnements en un tout cohérent. Les interactions de ces briques logicielles sont un enjeu majeur.
	\item L'évaluation pré-développement de certaines solutions, comme par exemple des possibilités qu'offrent les logiciels Raspberry-Pi de gestion vidéo et photo (\codeinline{text}{raspistill}, \codeinline{text}{raspivid}, etc.).
	\end{itemize}

\vspace{1cm}

Concernant les interfaces du système d'exploitation~:
\begin{itemize}[label=$\bullet$]
	\item Il existe une interface FTP destinée uniquement à récupérer les clichés du ciel stockés sur le télescope. L'utilisateur \codeinline{text}{autoscope} est le seul à pouvoir se connecter au serveur FTP et il ne sert qu'à ça.
	\item Il existe une interface SSH destinée uniquement à l'administration système du télescope. L'utilisateur \codeinline{text}{admin} est le seul à pouvoir se connecter au serveur SSH.
	\item L'utilisateur \codeinline{text}{root} n'est accessible que localement ou à distance via l'utilisateur \codeinline{text}{admin}.
	\item La console locale \codeinline{text}{tty1} est la console d'accueil du système. Elle est la seule à disposer d'un terminal.
	\item La console locale \codeinline{text}{tty2} affiche les messages générés par le système d'exploitation et notamment les messages du système d'initialisation.
	\item La console locale \codeinline{text}{tty3} affiche les messages générés par le daemon d'interface avec le GPS \codeinline{text}{mtk3339d}.
	\item La console locale \codeinline{text}{tty4} affiche les messages générés par le daemon \codeinline{text}{helloworld} s'il est présent.
	\end{itemize}

\section{Support de la caméra}

Pour gérer les différentes configurations matérielles de façon plus "userfriendly", la\\Raspberry-Pi dispose d'un fichier de configuration \codeinline{text}{config.txt} que le $bootloader$ interprétera pour sélectionner les $overlays$ correspondants et composer le $devicetree$ qui convient à l'architecture matérielle utilisée. Celui-ci étant ensuite passé au $kernel$ lors du démarrage.

%\vspace{1cm}

Cette subtilité propre aux Raspberry-Pi permet à l'utilisateur de ne pas avoir besoin d'avoir affaire au $devicetree$ quand il s'agit de configuration. Par exemple l'activation du support d'un élément courant sur les Raspberry-Pi comme le module Raspicam.

%\vspace{1cm}

le logiciel \codeinline{text}{raspi-config} n'est autre qu'une interface à ce fichier de configuration.

\vspace{1cm}

Pour activer le support matériel de la caméra, il faut ajouter les lignes suivantes à ce fichier~:

%\code{ruby}
\code{bash}
start_x=1
gpu_mem=128
\end{minted}

%À travers Yocto, cela passe par l'ajout des lignes ci-dessous au fichier \codeinline{text}{local.conf} et donc à son modèle le fichier \codeinline{text}{meta-autoscope/conf/local.conf.sample} dans la $layer$ dédiée au projet.

À travers Yocto, le fichier \codeinline{text}{config.txt} est généré par la recette\\\codeinline{text}{meta-raspberrypi/recipes-bsp/bootfiles/rpi-config_git.bb}.

On la surcharde donc, dans la $layer$ dédiée au projet, de la recette\\\mintinline[fontsize=\footnotesize]{text}{meta-autoscope/recipes-bsp/bootfiles/rpi-config_%.bb}~:

\code{bash}
VIDEO_CAMERA = "1"
GPU_MEM = "128"
\end{minted}

\vspace{1cm}

Quant à l'utilisation de la caméra, il existe des logiciels tels que \codeinline{text}{raspivid} pour filmer ou \codeinline{text}{raspistill} pour prendre des clichés. Tous deux font partie de la suite \codeinline{text}{userland} que l'on ajoute à notre image via la ligne ci-dessous dans le fichier\\\codeinline{text}{meta-autoscope/recipes-autoscope/images/autoscope-console-image.bb}~:

\code{bash}
IMAGE_INSTALL += "userland"
\end{minted}

À l'usage, la commande suivante permet d'afficher en plein écran le flux vidéo jusqu'à ce qu'on le stoppe~:

\code{text}
root@autoscope ~ #
    raspivid -t 0
\end{minted}

\section{Étude du transfert du flux vidéo sur le réseau}

Pour l'instant seul un test a été réalisé. Il s'agit d'afficher sur un ordinateur distant le flux vidéo filmé par la Raspberry-Pi. On utilise pour cela \codeinline{text}{netcat}.

\code{text}
~ $
    nc -l -p 5001 | /usr/bin/mplayer -fps 10 -cache 1024 -

root@autoscope ~ #
    raspivid -fps 10 -t 0 -o - | nc <ip.de.l'ordinateur> 5001
\end{minted}

\vspace{1cm}

La procédure fonctionne, le lecteur \codeinline{text}{mplayer} s'ouvre et lit la vidéo, toutefois malgré le taux de rafraîchissement très faible ($10fps$), une latence particulièrement longue existe, de l'ordre de 2 à 10 secondes.

\vspace{1cm}

Confronté à une problématique similaire sur un projet différent, un autre étudiant a réussi à transférer le flux vidéo à un périphérique quelconque sans latence en utilisant la librairie Python \codeinline{text}{picamera} et le programme disponible ici~:

{\href{http://picamera.readthedocs.io/en/latest/recipes2.html#web-streaming}{\codeinline{text}{http://picamera.readthedocs.io/en/latest/recipes2.html#web-streaming}}}

\vspace{1cm}

Celui-ci semble être similaire mais dénué de l'interface web. Il est une piste intéressante à explorer et probablement la solution la plus simple pour mettre en œuvre le système. L'existence d'une librairie similaire ou d'une solution alternative en C/C++ serait tout de même préférable car elle affranchirait du besoin d'inclure dans le système d'exploitation toutes les librairies Python nécessaires à ce programme.

{\href{https://picamera.readthedocs.io/en/latest/recipes2.html#rapid-capture-and-streaming}{\codeinline{text}{https://picamera.readthedocs.io/en/latest/recipes2.html#rapid-capture-and-stre}\\\codeinline{text}{aming}}}

\section{Splash screen}

Le système d'exploitation disposait déjà d'un écran de démarrage aux couleurs de l'école survenant lors de la phase d'initialisation du système.

Un second a été ajouté lors de la phase précédente, le démarrage du kernel, c'est-à-dire de Linux. Cela n'a pas vraiment d'intérêt pour le télescope si ce n'est un peu d'esthétique lorsqu'il démarre avec un écran branché. Cependant cela met en œuvre un processus qui sera utile pour d'autres choses, la configuration du kernel.

\vspace{1cm}

Les éléments des sources de Linux impliqués dans le splash screen sont les suivants~:
\begin{itemize}[label=$\bullet$]
	\item Dans le dossier \codeinline{text}{kernel-source/drivers/video/logo/}
	\begin{itemize}
		\item \codeinline{text}{Makefile}
		\item \codeinline{text}{Kconfig}
		\item \codeinline{text}{logo.c}
		\item Différents fichiers image, ceux nous intéressant sont au format \codeinline{text}{logo_*_clut224.ppm}
		\end{itemize}
	\item Dans le dossier \codeinline{text}{kernel-source/include/linux/}
	\begin{itemize}
		\item \codeinline{text}{linux_logo.h}
		\end{itemize}
	\end{itemize}

\vspace{1cm}

Tout d'abord l'on crée une recette yocto de surcharge de la recette kernel utilisée par la \codeinline{text}{meta-raspberrypi}. Voici l'allure du dossier associé à la recette. À noter que l'arborescence utilisée par une recette de surcharge du kernel est plus sensible qu'une recette de surcharge quelconque.

\code{text}
~/yocto/sources/meta-autoscope $ tree recipes-kernel/
    recipes-kernel/
    └── linux/
        ├── linux-raspberrypi/
        │   └── raspberrypi3/
        └── linux-raspberrypi_%.bbappend
\end{minted}

\vspace{1cm}

Ensuite l'on crée l'image qui servira d'écran de démarrage, en commencant par lui donner les dimensions souhaitées, ici $1822\times 900$. Il faut alors la convertir au format qui convient~:

\code{text}
jpegtopnm lune-1822x900.jpg | ppmquant 224 | pnmnoraw > logo_autoscope_clut224.ppm 
mv logo_autoscope_clut224.ppm ~/yocto/sources/meta-autoscope/recipes-kernel/linux/linux-raspberrypi/raspberrypi3/
\end{minted}

\vspace{1cm}

Puis des lignes sont à ajouter dans les sources du kernel dont la localisation dans l'arborescence yocto est la suivante~:
\codeinline{text}{~/yocto/build/tmp/work-shared/raspberrypi3/kernel-source/}

\vspace{1cm}

\codeinline{text}{include/linux/linux_logo.h}~:
\code{C}
extern const struct linux_logo logo_autoscope_clut224;
\end{minted}

%\vspace{1cm}

\codeinline{text}{drivers/video/logo/logo.c}~:
\code{C}
#ifdef CONFIG_LOGO_AUTOSCOPE_CLUT224
        /* Autoscope Linux logo */
        logo = &logo_autoscope_clut224;
#endif
\end{minted}

%\vspace{1cm}

\codeinline{text}{drivers/video/logo/Makefile}~:
\code{makefile}
obj-$(CONFIG_LOGO_AUTOSCOPE_CLUT224)    += logo_autoscope_clut224.o
\end{minted}

%\vspace{1cm}

\codeinline{text}{drivers/video/logo/Kconfig}~:
\code{kconfig}
config LOGO_AUTOSCOPE_CLUT224
    bool "224-color Autoscope Linux logo"
    default y

\end{minted}

%\vspace{1cm}

On réalise un patch de ces modifications~:

\code{text}
~/yocto/build/tmp/work-shared/raspberrypi3/kernel-source $
    git add drivers/video/logo/{Kconfig,Makefile,logo.c} incude/linux/linux_logo.h
    git commit -m "Autoscope logo"
    git format-patch -1
    mv 0001-Autoscope-logo.patch ~/yocto/sources/meta-autoscope/recipes-kernel/linux/linux-raspberrypi/raspberrypi3/
\end{minted}

\vspace{1cm}

On configure ensuite le kernel afin d'activer l'écran de démarrage et de choisir celui souhaité. On réalise pour cela un $fragment$ de configuration~:

\codeinline{text}{meta-autoscope/recipes-kernel/linux/linux-raspberrypi/raspberrypi3/logo.cfg}~:
\code{C}
CONFIG_LOGO=y
CONFIG_LOGO_LINUX_MONO=y
CONFIG_LOGO_LINUX_VGA16=y
# CONFIG_LOGO_LINUX_CLUT224 is not set
CONFIG_LOGO_AUTOSCOPE_CLUT224=y
\end{minted}

\vspace{1cm}

La dernière étape est d'écrire la recette pour prendre en compte toutes ces modifications~:

\codeinline{text}{meta-autoscope/recipes-kernel/linux/linux-raspberrypi_\%.bbappend}~:
\code{bash}
FILESEXTRAPATHS_prepend := "${THISDIR}/${PN}:"

SRC_URI_append_raspberrypi3 += " \
    file://0001-Autoscope-logo.patch \
    file://logo.cfg \
    file://logo_autoscope_clut224.ppm \
    "

do_patch_prepend() {
    cp ${WORKDIR}/logo_autoscope_clut224.ppm ${S}/drivers/video/logo/
}
\end{minted}

\vspace{1cm}
Voici donc l'arborescence associée à la recette~:

\code{text}
~/yocto/sources/meta-autoscope $ tree recipes-kernel/
    recipes-kernel/
    └── linux/
        ├── linux-raspberrypi/
        │   └── raspberrypi3/
        │       ├── 0001-Autoscope-logo.patch
        │       ├── logo_autoscope_clut224.ppm
        │       └── logo.cfg
        └── linux-raspberrypi_%.bbappend
\end{minted}

\vspace{1cm}

Après une longue phase de compilation puisque le kernel est recompilé, on observe au démarrage la succession des deux écrans de démarrages~:

\begin{figure}[H]
    \centering
    
    
    \decoRule
    \caption[
    Écrans de démarrage du noyau Linux à droite et du processus d'initialisation à gauche]{
    Écrans de démarrage du noyau Linux à droite et du processus d'initialisation à gauche}
    \label{fig:Écrans de démarrage du noyau Linux à droite et du processus d'initialisation à gauche}
    \end{figure}

\vspace{1cm}

Les messages provenant du kernel s'affichent par dessus l'écran de démarrage et "polluent" l'écran d'accueil. Il est possible de les masquer en passant l'argument \codeinline{text}{quiet} au kernel lorsque le bootloader l'invoque. L'argument \codeinline{text}{console=tty2} permet de rediriger les messages provenant du processus d'initialisation vers la console \codeinline{text}{/dev/tty2} accessible par la combinaison de touches \codeinline{text}{[CTRL]}, \codeinline{text}{[ALT]}, \codeinline{text}{[F2]}.

Sur Raspberry-Pi, les arguments passés au kernel sont partiellement stockés dans le fichier \codeinline{text}{cmdline.txt}. Pour le modifier depuis Yocto, on ajoute la ligne suivante à la recette

\mintinline[fontsize=\footnotesize]{text}{meta-autoscope/recipes-kernel/linux/linux-raspberrypi_%.bbappend}~:
\code{bash}
CMDLINE_append = "quiet console=tty2"
\end{minted}

\begin{figure}[H]
    \centering
    
    
    \decoRule
    \caption[
    Écran de démarrage du noyau Linux à droite et écran d'accueil à gauche]{
    Écran de démarrage du noyau Linux à droite et écran d'accueil à gauche}
    \label{fig:Écran de démarrage du noyau Linux à droite et écran d'accueil à gauche}
    \end{figure}

\section{Hotspot Wifi}

Configurer le télescope en Hotspot Wifi est une solution intéressante car ainsi un appareil client peut s'y connecter sans qu'il n'y ait besoin d'une infrastructure existante, un réseau local par exemple.

Pour configurer la Raspberry-Pi en Hotspot, deux choses sont nécessaires~:
\begin{itemize}[label=$\bullet$]
	\item Configurer le kernel pour qu'il supporte le mode \codeinline{text}{tether}.
	\item Le logiciel \codeinline{text}{connman}
	\end{itemize}

\codeinline{text}{meta-autoscope/recipes-kernel/linux/linux-raspberrypi/raspberrypi3/hotspot.cfg}~:
\code{c}
CONFIG_BRIDGE=m
CONFIG_IP_NF_TARGET_MASQUERADE=m
CONFIG_NETFILTER=m
CONFIG_NF_CONNTRACK_IPV4=m
CONFIG_NF_NAT_IPV4=m

CONFIG_IP_NF_IPTABLES=m
CONFIG_IP_MULTIPLE_TABLES=m
CONFIG_NETFILTER_NETLINK_ACCT=m
CONFIG_NETFILTER_XT_MATCH_NFACCT=m
CONFIG_NETFILTER_XT_CONNMARK=m
CONFIG_NETFILTER_XT_TARGET_CONNMARK=m
CONFIG_NETFILTER_XT_MATCH_CONNMARK=m
\end{minted}

\mintinline[fontsize=\footnotesize]{text}{meta-autoscope/recipes-kernel/linux/linux-raspberrypi_%.bbappend}~:
\code{bash}
SRC_URI_append_raspberrypi3 += " \
    file://0001-Autoscope-logo.patch \
    file://logo.cfg \
    file://hotspot.cfg \
    file://logo_autoscope_clut224.ppm \
    "
\end{minted}

\codeinline{text}{meta-autoscope/recipes-autoscope/images/autoscope-console-image.bb}~:
\code{bash}
HOTSPOT = " \
    connman \
    connman-client \
    iptables \
"

IMAGE_INSTALL += " \
    ${CAMERA} \
    ${HOTSPOT} \
"
\end{minted}

\vspace{1cm}

Si l'on effectue les commandes suivantes, la Raspberry-Pi devient visible sur le réseau~:
%    sysctl -w net.ipv4.ip_forward=1
\code{text}
root@autoscope ~ #
    connmanctl enable wifi
    connmanctl tether wifi on Autoscope 123456789
\end{minted}

\vspace{1cm}

Pour automatiser le processus au démarrage, il faut utiliser le paquet \codeinline{text}{connman-conf} et remplir quelques fichiers de configuration~:

\codeinline{text}{meta-autoscope/recipes-autoscope/images/autoscope-console-image.bb}~:
\code{bash}
HOTSPOT = " \
    connman \
    connman-client \
    connman-conf \
    iptables \
"
\end{minted}

\codeinline{text}{meta-autoscope/recipes-connectivity/connman-conf/files/main.conf}~:
\code{bash}
[General]
DefaultAutoConnectTechnologies=wifi
TetheringTechnologies=wifi
PersistentTetheringMode=true
\end{minted}

\codeinline{text}{meta-autoscope/recipes-connectivity/connman-conf/files/settings}~:
\code{bash}
[global]
OfflineMode=false

[WiFi]
Enable=true
Tethering=true
Tethering.Identifier=Autoscope
Tethering.Passphrase=123456789

[Wired]
Enable=true
Tethering=false

[P2P]
Enable=false
Tethering=false
\end{minted}

\codeinline{text}{meta-autoscope/recipes-connectivity/connman-conf/connman-conf.bbappend}~:
\code{bash}
FILESEXTRAPATHS_prepend := "${THISDIR}/files:"

SRC_URI += " \
    file://main.conf \
    file://settings \
"

FILES_${PN} += "${sysconfdir}/*"

do_install_append() {
    install -d ${D}${sysconfdir}/connman/
    install -m 0755 ${WORKDIR}/main.conf ${D}${sysconfdir}/connman/main.conf
    install -d ${D}${localstatedir}/lib/connman/
    install -m 0755 ${WORKDIR}/settings ${D}${localstatedir}/lib/connman/settings
}
\end{minted}

Les lignes ajoutées à \codeinline{text}{do_install()} permettent de déplacer les fichiers à leur place dans l'arborescence du système~:
\begin{itemize}[label=$\bullet$]
	\item \codeinline{text}{/etc/connman/main.conf}
	\item \codeinline{text}{/var/lib/connman/settings}
	\end{itemize}

\vspace{1cm}

À noter que sans la ligne \codeinline{text}{FILES_${PN} += "${sysconfdir}/*"}, Bitbake est incapable de connaître cette variable et donc de déplacer le fichier. La question ne se pose pas pour la variable \codeinline{text}{localstatedir} puisque l'on trouve la ligne suivante\\\codeinline{text}{FILES_${PN} = "${localstatedir}/* ${datadir}/*"} dans la recette originale~:\\\codeinline{text}{poky/meta/recipes-connectivity/connman-conf/connman-conf.bb}

\vspace{1cm}

%Quant à la commande \codeinline{text}{sysctl -w net.ipv4.ip_forward=1} qui n'est pas à effectuer à chaque démarrage, on peut l'automatiser ainsi~:
%
%\codeinline{text}{meta-autoscope/recipes-autoscope/images/autoscope-console-image.bb}~:
%\code{bash}
%hotspot() {
%    echo 'net.ipv4.ip_forward = 1' >> ${IMAGE_ROOTFS}/etc/sysctl.conf
%}
%
%ROOTFS_POSTPROCESS_COMMAND += " hotspot; "
%\end{minted}

\vspace{1cm}

Ainsi, dès le démarrage de la Raspberry-Pi, le Hotspot \codeinline{text}{Autoscope} est visible depuis un équipement Wifi. Le mot de passe est \codeinline{text}{123456789}.

\begin{figure}[H]
    \centering
    
    \decoRule
    \caption[
    Connexion à la Raspberry-Pi depuis un ordinateur distant]{
    Connexion à la Raspberry-Pi depuis un ordinateur distant}
    \label{fig:Connexion à la Raspberry-Pi depuis un ordinateur distant}
    \end{figure}

\section{Serveur FTP}

Plusieurs serveurs FTP sont disponibles dans Poky, \codeinline{text}{vsftpd} semble être une bonne solution pour sa légèreté, sa fiabilité et ses possibilités de configuration.

\codeinline{text}{meta-autoscope/recipes-autoscope/images/autoscope-console-image.bb}~:
\code{bash}
FTP = " \
    vsftpd \
"

IMAGE_INSTALL += " \
    ${CAMERA} \
    ${HOTSPOT} \
    ${FTP} \
"
\end{minted}

\codeinline{text}{meta-autoscope/recipes-connectivity/vsftpd/vsftpd_\%.bbappend}~:
\code{bash}
FILESEXTRAPATHS_prepend := "${THISDIR}/files:"
\end{minted}

\codeinline{text}{meta-autoscope/recipes-connectivity/vsftpd/files/vsftpd.user_list}~:
\code{bash}
autoscope
\end{minted}

\codeinline{text}{meta-autoscope/recipes-connectivity/vsftpd/files/vsftpd.conf}~:
\code{bash}
listen=YES
anonymous_enable=NO
local_enable=YES
write_enable=YES
local_umask=022
dirmessage_enable=YES
xferlog_enable=YES
connect_from_port_20=YES
xferlog_std_format=YES
ftpd_banner=Welcome to Autoscope FTP service.
ls_recurse_enable=YES
pam_service_name=vsftpd
userlist_deny=NO
userlist_enable=YES
use_localtime=YES
chroot_local_user=YES
allow_writeable_chroot=YES
tcp_wrappers=YES
user_sub_token=$USER
local_root=/home/$USER
\end{minted}

Note~: Des commentaires explicatifs figurent dans le fichier \codeinline{text}{vsftpd.conf} mais ne sont pas affichés ici.

\vspace{1cm}

Le serveur est alors accessible depuis un navigateur web via l'URL \codeinline{text}{ftp://<ip.raspberry.pi>} ou plus simplement la commande \codeinline{text}{ftp autoscope@<ip.raspberry.pi>}. Le mot de passe de l'utilisateur \codeinline{text}{autoscope} est demandé.

\begin{figure}[H]
    \centering
    
    \decoRule
    \caption[
    Accès au serveur FTP de la Raspberry-Pi depuis un navigateur]{
    Accès au serveur FTP de la Raspberry-Pi depuis un navigateur}
    \label{fig:Accès au serveur FTP de la Raspberry-Pi depuis un navigateur}
    \end{figure}

\vspace{1cm}

\begin{itemize}[label=$\bullet$]
	\item \codeinline{text}{autoscope} est le seul utilisateur autorisé à accéder au serveur FTP.
	\item Le serveur se lance automatiquement lors de la phase d'initialisation du système.
	\item L'option \codeinline{text}{chroot_local_user=YES} du fichier \codeinline{text}{vsftpd.conf} empêche l'utilisateur de remonter dans l'arborescence du système au delà du dossier défini par l'option\\\codeinline{text}{local_root=/home/$USER}, c'est-à-dire \codeinline{text}{/home/autoscope}. Il s'agit là d'une mesure élémentaire de sécurité.
	\end{itemize}

\section{Driver helloworld}

Ce driver minimaliste a pour but de préparer le terrain pour les drivers des moteurs et de l'IMU.

\codeinline{text}{hello.c}~:
\code{C}
#include <linux/module.h>

int init_module(void)
{
    printk("Hello World!\n");
    return 0;
}

void cleanup_module(void)
{
    printk("Goodbye Cruel World!\n");
}

MODULE_LICENSE("GPL");
\end{minted}

\codeinline{text}{Makefile}~:
\code{makefile}
obj-m := hello.o

SRC := $(shell pwd)

all:
    $(MAKE) -C $(KERNEL_SRC) M=$(SRC)

modules_install:
    $(MAKE) -C $(KERNEL_SRC) M=$(SRC) modules_install

clean:
    rm -f *.o *~ core .depend .*.cmd *.ko *.mod.c
    rm -f Module.markers Module.symvers modules.order
    rm -rf .tmp_versions Modules.symvers
\end{minted}

Un fichier \codeinline{text}{COPYING} contient une licence GPL.

\vspace{1cm}

Tous ces fichiers figurent sur une branche dédiée \codeinline{text}{hello_mod} du dépôt~:\\\codeinline{text}{github.com/thibaudledo/Autoscope}.

\vspace{1cm}

\codeinline{text}{meta-autoscope/recipes-test/hello-mod/hello-mod_git.bb}~:
\code{bash}
SUMMARY = "Example of how to build an external Linux kernel module"
LICENSE = "GPLv2"
LIC_FILES_CHKSUM = "file://${COREBASE}/meta/COPYING.GPLv2;md5=751419260aa954499f7abaabaa882bbe"

inherit module

SRC_URI = "git://github.com/thibaudledo/Autoscope;protocol=git;branch=hello_mod"

SRCREV = "${AUTOREV}"
S = "${WORKDIR}/git"

RPROVIDES_${PN} += "kernel-module-hello"
\end{minted}

\codeinline{text}{meta-autiscope/recipes-autoscope/images/autoscope-console-image.bb}~:
\code{bash}
HELLOWORLD = " \
    hello-mod \
" 

IMAGE_INSTALL += " \
    ${CAMERA} \
    ${HOTSPOT} \
    ${FTP} \
    ${HELLOWORLD} \
"
\end{minted}

\vspace{1cm}

Ainsi avec les commandes suivantes on observe les messages d'init et de cleanup s'afficher~:
\code{text}
root@autoscope ~ #
    modprobe hello
        [  xx.xxxxxx] hello: loading out-of-tree module taints kernel.
        [  xx.xxxxxx] Hello World!
    rmmod hello
        [  xx.xxxxxx] Goodbye Cruel World!
\end{minted}

\vspace{1cm}

Pour travailler localement, ce qui est utile en phase de développement, il suffit de cloner le dépôt du driver~:

\code{text}
~/yocto/sources/meta-autoscope/recipes-test/hello-mod $
    git clone https://github.com/thibaudledo/Autoscope -b hello_mod files/
\end{minted}

Et de créer une seconde recette où \codeinline{text}{SRC_URI} pointe vers les fichiers présents dans le dossier \codeinline{text}{files/}.

%TODO hello-mod_local? yocto choose version
\codeinline{text}{meta-autoscope/recipes-test/hello-mod/hello-mod-local.bb}~:
\code{bash}
SRC_URI = " \
    file://Makefile \
    file://COPYING \
    file://hello.c \
"
\end{minted}

\codeinline{text}{meta-autiscope/recipes-autoscope/images/autoscope-console-image.bb}~:
\code{bash}
HELLOWORLD = " \
    hello-mod-local \
"
\end{minted}

\section{Programme helloworld}

Ce programme a pour but de préparer le terrain pour le programme principal du télescope ainsi que pour d'éventuels programmes de test.

\codeinline{text}{meta-autoscope/recipes-test/helloworld/files/helloworld.c}~:
\code{c}
#include <stdio.h>
#include <unistd.h>

int main(void) {
    while(1) {
        printf("helloworld : TEST MESSAGE\n");
        usleep(2000000);
        }
    return(0);
    }
\end{minted}

\vspace{1cm}

En l'absence de \codeinline{text}{Makefile}, c'est à la recette de comporter les instructions de compilation du programme.

\codeinline{text}{meta-autoscope/recipes-test/helloworld/helloworld.bb}~:
\code{bash}
SUMMARY = "Helloworld program test"
SECTION = "base"
LICENSE = "GPLv2"
LIC_FILES_CHKSUM = "file://${COREBASE}/meta/COPYING.GPLv2;md5=751419260aa954499f7abaabaa882bbe"

SRC_URI = " \
    file://helloworld.c \
    "

do_compile () {
    ${CC} ${CFLAGS} ${LDFLAGS} ${WORKDIR}/helloworld.c -o ${WORKDIR}/helloworld
}

do_install () {
    install -d ${D}${bindir}
    install -m 0755 ${WORKDIR}/helloworld ${D}${bindir}/
}
\end{minted}

\codeinline{text}{meta-autiscope/recipes-autoscope/images/autoscope-console-image.bb}~:
\code{bash}
HELLOWORLD = " \
    hello-mod \
    helloworld \
" 

IMAGE_INSTALL += " \
    ${CAMERA} \
    ${HOTSPOT} \
    ${FTP} \
    ${HELLOWORLD} \
"
\end{minted}

\vspace{1cm}

À l'issue de la compilation on observe la présence du programme dans le dossier \codeinline{text}{/usr/bin} du \codeinline{text}{rootfs}~:

\code{text}
~/yocto/build/tmp/work/raspberrypi3-poky-linux-gnueabi/autoscope-console-image/1.0-r0/ rootfs $
    find . | grep helloworld
        ./usr/bin/helloworld
\end{minted}

Et à l'usage~:

\code{text}
root@autoscope ~ #
    helloworld
        helloworld : TEST MESSAGE
        helloworld : TEST MESSAGE
        helloworld : TEST MESSAGE
    ^C
\end{minted}

\section{Daemonisation du programme helloworld}

Pour faire d'un programme un daemon, c'est-à-dire un programme se lançant au démarrage de la machine et fonctionnant en tache de fond (comme le serveur FTP par exemple), il faut avoir recours au système d'initialisation de l'OS, ici il s'agit de SysVinit.

\vspace{1cm}

On écrit d'abord un script d'initialisation qui sera installé dans le dossier \codeinline{text}{/etc/init.d/} doté d'un bandeau d'entête où figurent notamment les runlevels dans lesquels le daemon doit être invoqué et ceux dans lesquels il doit être tué. Généralement un daemon peut être invoqué dans les runlevels $2$, $3$, $4$, $5$ et peut être tué dans les runlevels $0$, $1$, $6$. Généralement le runlevel $5$ est celui de fonctionnement normal de la machine, $0$ celui de l'arrêt et $6$ celui du redémarrage.

\codeinline{text}{meta-autoscope/recipes-test/helloworld/files/helloworld.sh}~:
\code{bash}
#!/bin/sh
### BEGIN INIT INFO
# Provides:             helloworld
# Required-Start:
# Required-Stop:
# Default-Start:        5
# Default-Stop:         0 1 6
# Short-Description:    Helloworld test
### END INIT INFO

NAME="helloworld"
DESC="Test program"
DAEMON="/usr/bin/${NAME}"
PIDFILE="/var/run/${NAME}.pid"

case "$1" in
    start)
        echo -n "Starting ${DESC}: ${NAME}... "
#       start-stop-daemon -S -b -C -q -x ${DAEMON} > /dev/tty3 #-C don't work with busybox
        ${DAEMON} > /dev/tty4 &
        echo $! > ${PIDFILE}
        echo "done"
        ;;
    stop)
        echo -n "Stopping ${DESC}: ${NAME}... "
        start-stop-daemon -K -q -x ${DAEMON}
        rm -f ${PIDFILE}
        echo "done"
        ;;
    restart)
        $0 stop
        $0 start
        ;;
    status)
        if [ "`pidof ${DAEMON}`" ]
        then
            echo "Program ${NAME} is running (`pidof ${DAEMON}`)."
        else
            echo -n "Program ${NAME} is not running"
            ls ${PIDFILE} &> /dev/null && echo -n " and the pidfile exists" ; echo "."
            fi
        ;;
    *)
        echo "Usage: $0 {start|stop|restart|status}"
        exit 1
        ;;
    esac
exit 0
\end{minted}

Les messages produits par le daemon sont redirigés vers la console \codeinline{text}{/dev/tty4} accessible par la combinaison de touches \codeinline{text}{[CTRL]}, \codeinline{text}{[ALT]}, \codeinline{text}{[F4]}.

\vspace{1cm}

La recette yocto est légèrement différente.

\codeinline{text}{meta-autoscope/recipes-test/helloworld/helloworld-daemon.bb}~:
\code{bash}
SUMMARY = "Helloworld daemon test"
SECTION = "base"
LICENSE = "GPLv2"
LIC_FILES_CHKSUM = "file://${COREBASE}/meta/COPYING.GPLv2;md5=751419260aa954499f7abaabaa882bbe"

SRC_URI = " \
    file://helloworld.sh \
    file://helloworld.c \
    "
inherit update-rc.d

do_compile () {
    ${CC} ${CFLAGS} ${LDFLAGS} ${WORKDIR}/helloworld.c -o ${WORKDIR}/helloworld
}

do_install () {
    install -d ${D}${sysconfdir}/init.d
    cat ${WORKDIR}/helloworld.sh | \
      sed -e 's,/etc,${sysconfdir},g' \
          -e 's,/usr/sbin,${sbindir},g' \
          -e 's,/var,${localstatedir},g' \
          -e 's,/usr/bin,${bindir},g' \
          -e 's,/usr,${prefix},g' > ${D}${sysconfdir}/init.d/helloworld
    chmod a+x ${D}${sysconfdir}/init.d/helloworld

    install -d ${D}${bindir}
    install -m 0755 ${WORKDIR}/helloworld ${D}${bindir}/
}

INITSCRIPT_NAME = "helloworld"
INITSCRIPT_PARAMS = "start 99 5 . stop 00 0 1 6 ."
\end{minted}

\codeinline{text}{meta-autoscope/recipes-autoscope/images/autoscope-console-image.bb}~:
\code{bash}
HELLOWORLD = " \
    hello-mod \
    helloworld-daemon \
" 

IMAGE_INSTALL += " \
    ${CAMERA} \
    ${HOTSPOT} \
    ${FTP} \
    ${HELLOWORLD} \
"
\end{minted}

\vspace{1cm}

On observe ensuite dans le \codeinline{text}{rootfs} la présence du script d'initialisation ainsi que la présence d'un lien symbolique vers celui-ci dans les dossiers des runlevels 0, 1, 5, 6 avec des préfixes~:
\begin{itemize}[label=$\bullet$]
	\item \codeinline{text}{S} ou \codeinline{text}{K} indiquant si le daemon est invoqué (Start) ou tué (Kill).
	\item \codeinline{text}{00} à \codeinline{text}{99} indiquant le numéro de priorité de l'appel, \codeinline{text}{00} étant le plus prioritaire.
	\end{itemize}

\code{text}
~/yocto/build/tmp/work/raspberrypi3-poky-linux-gnueabi/autoscope-console-image/1.0-r0/ rootfs $
    find . | grep helloworld
        ./usr/bin/helloworld
        ./etc/init.d/helloworld
        ./etc/rc0.d/K00helloworld
        ./etc/rc1.d/K00helloworld
        ./etc/rc5.d/S99helloworld
        ./etc/rc6.d/K00helloworld
\end{minted}

\vspace{1cm}

Et à l'usage~:

\code{text}
root@autoscope ~ #
    /etc/init.d/helloworld status
        Program helloworld is running (347).

    # [CTRL] [ALT] [F3]
        helloworld : TEST MESSAGE
        helloworld : TEST MESSAGE
        helloworld : TEST MESSAGE

    # [CTRL] [ALT] [F1]
    /etc/init.d/helloworld stop
        Stopping Test program: helloworld... done
    /etc/init.d/helloworld status
        Program helloworld is not running.
\end{minted}

\section{Support de la liaison UART et communication avec le GPS}

Pour activer le support de la liaison UART, il faut ajouter la ligne suivante au fichier \codeinline{text}{config.txt}
\code{bash}
enable_uart=1
\end{minted}

C'est-à-dire la ligne suivante à la recette

\mintinline[fontsize=\footnotesize]{text}{meta-autoscope/recipes-bsp/bootfiles/rpi-config_%.bbappend}~:
\code{bash}
ENABLE_UART = "1"
\end{minted}

Remarque~: Ce genre de variables de configurations propre aux Raspberry-Pi est généralement utilisé via les fichiers \codeinline{text}{local.conf} ou \codeinline{text}{distro.conf}. La raison en est que certaines, comme \codeinline{text}{ENABLE_UART} justement, ont un effet dans plusieurs recettes. Celle-ci, par le biais de la recette \mintinline[fontsize=\footnotesize]{text}{linux-raspberrypi_%.bb} ajoute également \codeinline{text}{console=serial0,115200} au fichier \codeinline{text}{cmdline.txt}. Ce fichier contient les arguments qu'U-Boot passe à Linux lorsqu'il l'appelle. Dans notre cas cette ligne n'est pas souhaitable, on peut donc placer la variable dans une surcharge de la recette \mintinline[fontsize=\footnotesize]{text}{rpi-config_%.bb}

\vspace{1cm}

%On observe que désormais le fichier \codeinline{text}{/dev/ttyS0} existe, avant cela seul \codeinline{text}{/dev/ttyAMA0} existait, autre ligne UART utilisée par le module Bluetooth de la Raspberry-pi.
De plus sur la Raspberry-Pi 3, il existe une UART classique attribuée par défaut au module Bluetooth de la carte et une "miniUART" qui peut poser problème à l'utilisation puisqu'elle n'a pas d'horloge interne et dépend de l'horloge du processeur qui varie selon sa charge. Quelques essais ont confirmé que cette UART posait problème.

Il existe une overlay du device tree permettant d'intervertir les deux UARTs\\\codeinline{text}{pi3-disable-bt-overlay.dts} et de relier l'UART classique aux pins \codeinline{text}{8} et \codeinline{text}{10} du connecteur. L'on active l'overlay ainsi~:

\mintinline[fontsize=\footnotesize]{text}{meta-autoscope/recipes-bsp/bootfiles/rpi-config_%.bbappend}
\code{bash}
RPI_EXTRA_CONFIG = "\n\
dtparam=act_led_trigger=off\n\
disable_camera_led=1\n\
dtoverlay=pi3-disable-bt\n\
"
\end{minted}

Remarque~: Cette overlay ne semble pas fonctionner avec U-boot comme bootloader. Aucune solution n'a encore été trouvée pour les faire fonctionner ensemble.

\vspace{1cm}

%Si l'on boucle la ligne \codeinline{text}{Tx} sur \codeinline{text}{Rx} et que l'on observe à l'analyseur logique, voici la trame observée pour une écriture quelconque sur la ligne.

%\code{text}
%root@autoscope ~ #
%    echo "5A" | microcom /dev/ttyS0 -s 9600
%        5A
%\end{minted}

%\begin{figure}[H]
%    \centering
%    \includegraphics[width=1\linewidth]{\figures/osc_uart.png}
%    \decoRule
%    \caption[
%    Trame UART relevée à l'analyseur logique]{
%    Trame UART relevée à l'analyseur logique}
%    \label{fig:Trame UART relevée à l'analyseur logique}
%    \end{figure}

%\vspace{1cm}

%On retrouve les trois caractères ASCII envoyés par la commande \codeinline{text}{echo}. Ceux-ci réapparaissant également à l'écran, démontrant le fonctionnement de la liaison en lecture et en écriture.

Si l'on connecte le GPS à la carte, on peut lui envoyer une trame l'interrogeant sur les informations de son firmware \codeinline{text}{605 PMTK_Q_RELEASE}.

\code{text}
root@autoscope ~ #
    echo -ne "\$PMTK605*31\r\n" | microcom /dev/ttyAMA0 -s 9600
        $PMTK705,AXN_2.31_3339_13101700,5632,PA6H,1.0*6B
        $GPGGA,000700.800,,,,,0,00,,,M,,M,,*77
        $GPGSA,A,1,,,,,,,,,,,,,,,*1E
        $GPRMC,000700.800,V,,,,,0.00,0.00,060180,,,N*4D
        $GPVTG,0.00,T,,M,0.00,N,0.00,K,N*32
        $GPGGA,000701.800,,,,,0,00,,,M,,M,,*76
        $GPGSA,A,1,,,,,,,,,,,,,,,*1E
        $GPGSV,1,1,00*79
        $GPRMC,000701.800,V,,,,,0.00,0.00,060180,,,N*4C
        $GPVTG,0.00,T,,M,0.00,N,0.00,K,N*32
    ^C
\end{minted}

L'on observe la trame de réponse \codeinline{text}{705 PMTK_DT_RELEASE} indiquant le nom et la version du firmware \codeinline{text}{AXN_2.31_3339_13101700} accompagnés d'autres informations constructeurs.
L'on observe ensuite une suite de quelques trames NMEA envoyée périodiquement toutes les secondes.

\begin{figure}[H]
    \centering
    
%    \includegraphics[width=1\linewidth]{\figures/osc_uart2.png}
    
    
    \decoRule
    \caption[
    Trame UART relevée à l'analyseur logique]{
    Trame UART relevée à l'analyseur logique}
    \label{fig:Trames UART relevées à l'analyseur logique}
    \end{figure}

\section{Support du bus I2C et communication avec l'IMU}

Pour activer le support du bus I2C, il faut ajouter les lignes suivantes au fichier \codeinline{text}{config.txt}
\code{bash}
dtparam=i2c1=on
dtparam=i2c_arm=on
\end{minted}

C'est-à-dire la ligne suivante à la recette

\mintinline[fontsize=\footnotesize]{text}{meta-autoscope/recipes-bsp/bootfiles/rpi-config_%.bbappend}~:
\code{bash}
ENABLE_I2C = "1"
\end{minted}

\vspace{1cm}

On ajoute également la suite de test \codeinline{text}{i2c-tools}~:

\codeinline{text}{meta-autoscope/recipes-autoscope/images/autoscope-console-image.bb}~:
\code{bash}
IMAGE_INSTALL += " \
    ${CAMERA} \
    ${HOTSPOT} \
    ${FTP} \
    ${HELLOWORLD} \
    i2c-tools \
"
\end{minted}

\vspace{1cm}

Ensuite, pour pouvoir utiliser \codeinline{text}{i2c-tools}, il faut activer un driver~:

\code{text}
root@autoscope ~ #
    modprobe i2c_dev
        [  xx.xxxxxx] i2c /dev entries driver
\end{minted}

Remarque~: Il est possible de le charger dès le démarrage en utilisant la variable\\\codeinline{text}{KERNEL_MODULE_AUTOLOAD}. Celle-ci est utilisable dans la recette kernel ou dans la recette dudit module.

\mintinline[fontsize=\footnotesize]{text}{meta-autoscope/recipes-kernel/linux/linux-raspberrypi_%.bbappend}~:
\code{bash}
KERNEL_MODULE_AUTOLOAD_append = "i2c_dev"
\end{minted}

\vspace{1cm}

On connecte la centrale inertielle au bus I2C et l'on peut observer les périphériques présents sur le bus~:

\code{text}
root@autoscope ~ #
    i2cdetect -y 1
             0  1  2  3  4  5  6  7  8  9  a  b  c  d  e  f
        00:          __ __ __ __ __ __ __ __ __ __ __ __ __
        10: __ __ __ __ __ __ __ __ __ __ __ __ __ __ __ __
        20: __ __ __ __ __ __ __ __ __ __ __ __ __ __ __ __
        30: __ __ __ __ __ __ __ __ __ __ __ __ __ __ __ __
        40: __ __ __ __ __ __ __ __ __ __ __ __ __ __ __ __
        50: __ __ __ __ __ __ __ __ __ __ __ __ __ __ __ __
        60: __ __ __ __ __ __ __ __ 68 __ __ __ __ __ __ __
        70: __ __ __ __ __ __ __ __
\end{minted}

Une seule adresse est attribuée, il s'agit de la centrale inertielle. Il est dit dans sa documentation que le registre \codeinline{text}{WHO_AM_I} à l'adresse \codeinline{text}{0x75} contient invariablement la valeur \codeinline{text}{0x71}. On peut alors essayer de lire ce registre.

\code{text}
root@autoscope ~ #
    i2cget -y 1 0x68 0x75
        0x71
\end{minted}

\begin{figure}[H]
    \centering
    
    \decoRule
    \caption[
    Trame I2C relevée à l'analyseur logique]{
    Trame I2C relevée à l'analyseur logique}
    \label{fig:Trame I2C relevée à l'analyseur logique}
    \end{figure}

\vspace{1cm}

La communication entre la centrale inertielle et la Raspberry-Pi fonctionne.

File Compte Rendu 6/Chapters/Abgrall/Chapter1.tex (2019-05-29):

\chapter{Hardware moteur}

\section{Cahier des charges du mouvement}

Pour mouvoir le télescope dans des conditions optimales, il y a des contraintes spécifiques à respecter. Le télescope est un appareil qui se doit d'être très précis. Les mouvements étant assurés par les moteurs, il faut que ces derniers soient précis. Les critères à contrôler sont l'angle par pas et le nombre de pas.

Dans un souci de confort d'emploi le télescope doit pouvoir atteindre sa cible sans trop faire patienter l'utilisateur. Il a fallu faire un compromis entre la vitesse et la précision.

\section{Les moteurs}

Nous avons retenu deux type de moteurs~:

\begin{figure}[H]
    \centering
    
    
    \decoRule
    \caption[
    Moteur 17HM15-0904S et moteur S20STH30-0604A]{
    Moteur 17HM15-0904S et moteur S20STH30-0604A}
    \label{fig:Moteur 17HM15-0904S et moteur S20STH30-0604A}
    \end{figure}

Le premier a été choisi pour l'azimut et l'élévation car il a suffisamment de couple pour mouvoir le télescope, et avec précision. À l'origine, nous en avons trouvé un exemplaire sur les imprimantes 3D et nous avons vérifié s'il répondait à nos contraintes.

Le second est plus léger que le premier, moins puissant. Il est plus adapté pour changer le zoom au bout de la flèche du télescope. Il est indispensable de limiter le poids au bout de la flèche du télescope pour faciliter ses déplacements et surtout ne pas le déséquilibrer.

\section{Le contrôleur}

Le contrôleur est une carte qui à partir de fronts montants en entrée fait tourner un moteur pas à pas d'un angle précis. Cette carte A4988 opto-isolée permet l'entraînement de moteur pas à pas à micropistes Allegro A4988. Il est doté d'une protection contre les surintensités et la surchauffe, ainsi que de cinq résolutions différentes en micropas (jusqu'à 1/16 pas). Il fonctionne de $8V$ à $35V$ et peut fournir jusqu'à environ $1A$ par phase sans dissipateur de chaleur ni flux d'air forcé.

\begin{figure}[H]
    \centering
    
    \decoRule
    \caption[
    Photo du contrôleur A4988]{
    Photo du contrôleur A4988}
    \label{fig:Photo du contrôleur A4988}
    \end{figure}

\section{Validation des moteurs et du câblage}

\begin{figure}[H]
    \centering
    
    \decoRule
    \caption[
    Schéma de câblage d'un contrôleur moteur sur la Raspberry Pi]{
    Schéma de câblage d'un contrôleur moteur sur la Raspberry Pi}
    \label{fig:Schéma de câblage d'un contrôleur moteur sur la Raspberry Pi}
    \end{figure}

Durant ce test nous avons vérifié le bon fonctionnement du moteur et contrôleur moteur.

Pour nous assurer que les moteurs de rotation et inclinaison sont suffisamment coupleux et résistant nous avons placé une courroie autour de l'axe du moteur et au bout de cette dernière nous avons attaché une masse d'environ $10kg$.
Ce test fut un succès et nous avons validé le choix des moteurs.

\begin{figure}[H]
    \centering
    
    \decoRule
    \caption[
    Test de la puissance du moteur]{
    Test de la puissance du moteur}
    \label{fig:Test de la puissance du moteur}
    \end{figure}

Nous avons profité du test pour manuellement utiliser les modes de pas en appliquant aux entrées MS1, MS2, MS3 du $5V$ en suivant la documentation ci-dessous~:

\begin{figure}[H]
    \centering
    
    \decoRule
    \caption[
    Documentation microStep a4988]{
    Documentation microStep a4988}
    \label{fig:Documentation microStep a4988}
    \end{figure}

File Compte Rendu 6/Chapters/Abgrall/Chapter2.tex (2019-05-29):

\chapter{Driver commande des moteurs}

\section{Introduction}

Un driver est un programme développé avec un langage reconnu pour sa proximité avec le matériel, le langage C. Et c'est la raison d'être des drivers. Ces derniers font la passerelle entre les applications qui se trouvent dans la partie utilisateur (user-space) et le matériel.

\vspace{1cm}

Le plus simple des exemples est celui du clavier. Lorsque j'appuie sur une touche pour écrire ce rapport un contact électrique est émit et informe le micro-processeur qu'une touche à été appuyée. Puis un programme, le driver du clavier, viens contrôler les entrées pour savoir quelle touche a été pressé. Et envoie cette information au système d'exploitation pour que la lettre soit affichée.

\vspace{1cm}

Le driver moteur a pour mission de permettre de contrôler les moteurs d'azimut, d'élévation et de zoom du télescope. D'informer le logiciel principal de l'accomplissement d'une manœuvre, théoriquement (explication chapitre 13.2). Il assure la sécurité du système de pilotage à bas niveau. Le système de sécurité consiste à interrompre le mouvement d'élévation ou de zoom si ils atteignent leur fin de course, le mouvement d'azimut n'étant pas soumis à cette contrainte.

\section{Fonctionnalités du driver}

\begin{figure}[H]
    \centering
    
    \decoRule
    \caption[
    Schéma des entrées / sorties du driver moteur]{
    Schéma des entrées / sorties du driver moteur}
    \label{fig:Schéma des entrées / sorties du driver moteur}
    \end{figure}

\vspace{1cm}

La figure ci-dessus représente le driver contrôlant les moteurs. À gauche du bloc il y a les entrées et les sorties du driver d'un point de vue informatique.

\vspace{1cm}

Les entrées regroupent l'ensemble des données qu'attend le driver pour entreprendre une action, nous retrouvons de ce fait, le choix de l'action à réaliser, le nombre de pas à parcourir, et le sens de rotation et le choix du moteur. Les choix des actions à faire sont en gras à l'intérieur du bloc Driver. Comme vous pouvez le voir toutes les actions n'ont pas besoin de toutes les informations demandées en entré (comme l'action \codeinline{text}{stopOne}), dans ces cas seules les entrées nécessaires seront prises en comptes.

\vspace{1cm}

Concernant les sorties informatiques, il y a l'acquittement de réception qui a pour but de rassurer l'application en lui indiquant ce qu'il a reçu, ainsi l'application peut vérifier que les données envoyées sont correctes. Si il y a une erreur de communication l'application demande l'arrêt des moteurs et renvoi l'ordre ajusté (en prenant en compte le déplacement qui à été effectué dans l'erreur).

%\vspace{1cm}

Nous trouvons ensuite l'achèvement d'action, lorsque une action arrive a son terme (mouvement d'azimut, d'élévation, etc.), le driver l'indique à l'application, ainsi si jamais il y a un ajustement à effectuer elle renverra un ordre pour bien être placé. Et pour finir ce coté informatique, il y a le retour de code d'erreur qui survient lorsqu'un incident arrive dans le driver (ressource inaccessible (pin, timer, interruption, problème de fermeture driver ou d'ouverture, etc.).

\vspace{1cm}

Sur le dessus du driver nous trouvons 5 entrées (matérielles) capteurs. Chacun d'eux prévient de l'arrivée en butée d'un axe, excepté pour le capteur rotation azimutale qui indique juste la position du télescope en rotation lorsqu'il est activé.

Ce capteur a deux rôles, durant la phase de développement il nous permettra de déterminer le nombre exact et réel du pas pour un tour complet du télescope (ce qui permettra de développer l'algorithme de positionnement du télescope dans l'application principale). Le second rôle, plus tard, sera de faire du recalibrage de la centrale inertielle en cas de décalage entre les résultats de ce capteur et ceux de la centrale inertielle.

\vspace{1cm}

Au final à droite du bloc nous trouvons les sorties (matérielles) du driver. Ces dernières répètent le même chose pour chacun des 3 moteurs~: une pin pour le front montant pour lancer un pas moteur, le sens de rotation (0 ou 1), et 3 pins pour le choix du mode pas de rotation du moteur (pas complet, demi-pas, quart de pas, etc.).

\vspace{1cm}
  
Deux exemples de fonctionnement du driver avec ces entrées/sorties~:
\begin{itemize}[label=$\bullet$]
	\item Faire tourner le zoom de 50 pas dans le sens horaire~:
	\begin{enumerate}
		\item Réception des nombres de l'application [ 3 ; 50 ; 0 ] pour choisir la fonction zoom, nombre de pas, sens de rotation horaire.
		\item Envoi de l'accusé de réception, à l'application, contenant les nombres [ 3 ; 50 ; 0 ].
		\item Exécution de la fonction zoom avec les données [ 3 ; 50 ; 0 ] en argument.
		\item Écrit dans la sorte du moteur zoom sens de rotation: 0.
		\item Écrit en sortie de mode de pas du moteur zoom la configuration pour faire des pas complet. 
		\item Créer un timer qui va permettre de créer un front montant, tant que l'on n'a pas atteint le nombre de pas à parcourir.
		\item Si l'on a parcouru tous les pas complet et qu'il faut réaliser des pas plus fins, pour atteindre au plus près l'angle demandé, on change le mode de pas en 16ème de pas. 
		\item Une fois tous les 16ème de pas effectués on envoi de l'achèvement d'action contenant le nombre 1.
		\item Le driver réinitialise ses variables et ressources (timer, etc.).
		\item Mise en attente d'un nouvel ordre, la boucle est bouclée.
		\end{enumerate}
	\item Arrêter tout les moteurs
	\begin{enumerate}
		\item Envoi au driver le nombre 5 pour choisir la fonction \codeinline{text}{stopall}.
		\item Réception de l'accusé de réception contenant le nombre 5.
		\item Réinitialise les variables et ressources.
		\item Réception de l'achèvement d'action contenant le nombre 1.
		\end{enumerate}
	\end{itemize}

\vspace{1cm}

Une fois une manœuvre terminée le driver informe l'application que l'action demandée est arrivé à son terme. Cependant d'un point de vue driver moteur il n'y a pas de possibilité de vérifier si le télescope est bien placé là où on lui a demandé de se placer. Si une personne ou objet bloque le mouvement du télescope ou des moteurs ces derniers ne renverront pas d'avertissement. C'est donc la centrale inertielle qui contrôlera le bon placement du télescope.

\vspace{1cm}

Les capteurs de fin de course servent de sécurité, cette partie est indépendante du reste. Elle a pour but d'arrêter un moteur qui à atteint sa position maximale, hormis pour le capteur de rotation qui a pour utilité dans un premier temps de faire une interruption lorsque un tour complet.

Avec cette information on pourra déterminer le nombre de pas moteur qu'il faut faire pour faire un tour complet de télescope sur lui même. Et dans un second temps de donner un point de repère pour les recalibrages de la centrale inertielle.

\vspace{1cm}

Les sorties "Mode de pas moteur..." permettent de choisir dans quel mode de rotation doit tourner le moteur (pas complet, demi-pas, quart de pas, huitième de pas, seizième de pas). Augmenter la division de pas permet d'affiner la rotation afin d'atteindre l'angle le plus exact possible compte tenu de ce qui a été commandé. Ainsi lorsqu'un moteur a accompli environ 90\% de la distance à parcourir, on change le mode de pas afin d'arriver au plus proche de l'angle exact.

\section{Interactions avec le driver}

Le driver est utilisé à partir d'une application situé dans le user-space du Linux embarqué. Pour cela j'ai étudié et testées plusieurs solutions.

La première qui m'est venu à l'idée était d'utiliser l'IPC (inter process communication).

Une seconde plus archaïque m'est venu à l'idée, celle de partager un ficher entre le programme dans le user-space et du driver. Pour que le programme dans le user-space puisse transférer ses ordres. Cependant je trouve cette solution peu sécurisée.

La troisième solution qui m'a été proposée par Vincent POULAILLEAU est d'utiliser la fonction \codeinline{text}{ioctl}. C'est cette solution que j'ai retenu car elle est une technique très rodé dans le domaine car elle était déjà utilisé à la version 7 d'UNIX. 

\section{Intégration du driver}

Pour que le driver soit utilisable dans le Linux embarqué Yocto, j'ai créé deux recettes. L'une viens chercher dans le Github du projet les sources du driver, cette recette permet l'importation du driver lors du build du Yocto (avec la commande \codeinline{text}{bitbake}).

La seconde recette permet d'ajouter l'application d'interface avec le driver dans le user-space du Yocto. Pour lancer l'application dans le Yocto dans la Raspberry-Pi il suffira d'écrire dans le terminal (de la cible) le nom de l'application: \codeinline{text}{a4988-test}

\section{Validation des fonctionnalités de bases}

\begin{figure}[H]
    \centering
    
    
    \decoRule
    \caption[
    Schéma de câblage d'un contrôleur moteur sur la Raspberry Pi]{
    Schéma de câblage d'un contrôleur moteur sur la Raspberry Pi}
    \label{fig:Schéma de câblage d'un contrôleur moteur sur la Raspberry Pi}
    \end{figure}

\vspace{1cm}

Pour valider mon driver, je l'ai testé avec une Raspberry-Pi, un contrôleur moteur et un moteur.

\begin{figure}[H]
    \centering
    
    \decoRule
    \caption[
    Photo du banc de test]{
	Photo du banc de test}
    \label{fig:Photo du banc de test}
    \end{figure}

\vspace{1cm}

J'ai pu valider les fonctionnalités développées, cependant la vitesse max atteinte par le moteur contrôlé par le driver est inférieure à celle que l'on peut atteindre en contrôlant le moteur avec un générateur basse fréquence. Voici le résultat de la commande envoyée par la Raspberry Pi par la pin Step au contrôleur moteur pour faire avancer à chaque front montant le moteur de 1 pas.

\begin{figure}[H]
    \centering
    
    \decoRule
    \caption[
    Mesure à l'oscilloscope de la commande moteur générée]{
	Mesure à l'oscilloscope de la commande moteur générée}
    \label{fig:Mesure à l'oscilloscope de la commande moteur générée}
    \end{figure}

\vspace{1cm}

Après avoir étudié les résultats avec d'autres professeurs, j'ai conclu que la période minimale que je puisse atteindre soit de $20ms$ est normal. Cette limitation est due au fait que mon driver n'a pas la priorité des ressources dans le Linux. Et que le Linux a un cycle lecture/écriture des entrées/sorties limité. Pour améliorer cela il faudrait passer sur un Linux temps réel.

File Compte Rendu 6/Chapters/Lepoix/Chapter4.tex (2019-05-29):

\chapter{Daemon d'interface avec le GPS}

Sur Linux, il ne convient généralement pas de gérer les périphériques utilisant l'UART avec des drivers. En effet à la différence des bus de communications comme I2C ou SPI, l'UART dispose déjà d'un driver permettant d'envoyer et de recevoir des trames depuis l'espace utilisateur. Les drivers résidant eux dans l'espace du système d'exploitation.

De plus l'UART est d'un niveau d'abstraction supérieur par rapport à ces bus puisqu'il ne s'agit pas d'envoyer des commandes de lecture ou d'écriture sur les registres du périphérique mais d'envoyer des trames de commande que le périphérique va interpréter.

\vspace{1cm}

On utilise donc généralement des daemons pour faire l'interface avec ce type de périphériques. Les daemons étant des programmes tournant en tâche de fond de l'espace utilisateur du système.

%fonctionnement gps, trames NMEA
%configuration gps
\section{Fonctionnement du GPS}

Le GPS utilise des trames NMEA, qui est une norme de communication américaine pour les équipements marins. Elle est largement utilisée par les GPS.

\vspace{1cm}

Il existe de nombreuses trames NMEA, toutes sont préfixées de \codeinline{text}{$} et suffixées de \mintinline[fontsize=\footnotesize]{text}{\r\n}. Les deux premiers caractères après \codeinline{text}{$} désignent le type d'équipement qui émet la trame, une trame émise par un GPS commence par \codeinline{text}{GP}. Elles comportent également un CRC, calculé par XOR des codes ASCII des précédents caractères.

Ce GPS dispose également d'un jeu de trames propre au constructeur, composé de commandes et de réponses, commençant par \codeinline{text}{PMTK}.

\vspace{1cm}

Le GPS envoie périodiquement certaines trames NMEA et répond aux instructions que l'on peut lui envoyer.

Parmi les trames intéressantes qu'envoie le GPS, on trouve~:
\begin{itemize}[label=$\bullet$]
	\item \codeinline{text}{GPGLL}~: Contient notamment la latitude et la longitude.
	\item \codeinline{text}{GPRMC}~: Contient notamment la latitude et la longitude.
	\item \codeinline{text}{GPGGA}~: Contient notamment la latitude, la longitude et l'altitude.
	\item \codeinline{text}{PMTK705}~: Contient le nom et la version du firmware du GPS. Réponse à la trame de requête \codeinline{text}{PMTK605}.
	\end{itemize}

\vspace{1cm}

La trame \codeinline{text}{GPGGA} est celle qui contient le plus d'informations intéressantes. À titre d'exemple, voici sa décomposition~:

\mintinline[fontsize=\footnotesize]{text}{$GPGGA,204444.000,4042.6250,N,07400.5054,W,1,6,1.45,278.7,M,-34.2,M,,*6C\r\n}

\begin{itemize}[label=$\bullet$]
		\item \codeinline{text}{204444.000}~: Heure de calcul de la position $20h44m44s$
		\item \codeinline{text}{4042.6250,N}~: Latitude $40$°$42'62,50"$ Nord
		\item \codeinline{text}{07400.5054,W}~: Longitude $074$°$00'50,54"$ Est
		\item \codeinline{text}{1}~: Indicateur de qualité 1 = GPS
		\item \codeinline{text}{6}~: Nombre de satellites utilisés
		\item \codeinline{text}{1.45}~: Dilution de la position horizontale (HDOP)
		\item \codeinline{text}{278.7,M}~: Altitude par rapport au niveau moyen de la mer $278,7m$
		\item \codeinline{text}{-34.2,M}~: Hauteur du géoïde $-34,2m$
		\item \codeinline{text}{vide}~: Age des données GPS différentiel
		\item \codeinline{text}{vide}~: Identifient de la station GPS différentiel
		\item \codeinline{text}{6C}~: CRC de \codeinline{text}{GPGGA,204444.000,4042.6250,N,07400.5054,W,1,6,1.45,278.7,M,-34.2,M,,*}
		\end{itemize}

\vspace{1cm}

La trame \codeinline{text}{GPGGA} contenant toutes les informations utiles, il semble inutile de laisser le GPS envoyer périodiquement d'autres trames que celle-ci.

La trame de commande \codeinline{text}{314 PMTK_API_SET_NMEA_OUTPUT} permet de configurer les trames qu'envoie périodiquement le GPS~:

\mintinline[fontsize=\footnotesize]{text}{$PMTK314,0,0,0,1,0,0,0,0,0,0,0,0,0,0,0,0,0,0,0*29\r\n}

\begin{itemize}[label=$\bullet$]
	\item \codeinline{text}{GPGLL}~: Trame jamais envoyée.
	\item \codeinline{text}{GPRMC}~: Trame jamais envoyée.
	\item \codeinline{text}{GPVTG}~: Trame jamais envoyée.
	\item \codeinline{text}{GPGGA}~: Trame envoyée une fois tous les \codeinline{text}{1} calcul de position. Peut aller jusqu'à une trame tous les \codeinline{text}{5} calculs de position.
	\item \codeinline{text}{GPGSA}~: Trame jamais envoyée.
	\item \codeinline{text}{GPGSV}~: Trame jamais envoyée.
	\item Les autres champs doivent rester à \codeinline{text}{0}.
	\item \codeinline{text}{29}~: CRC de \codeinline{text}{PMTK314,0,0,0,1,0,0,0,0,0,0,0,0,0,0,0,0,0,0,0*}
	\end{itemize}

\vspace{1cm}

Le GPS doit alors répondre une trame \codeinline{text}{001 PMTK_ACK}~: \mintinline[fontsize=\footnotesize]{text}{$PMTK001,314,3*36\r\n} signifiant que la commande a été prise en compte.

\section{Fonctionnement du daemon}

\begin{figure}[H]
    \centering
    
    \decoRule
    \caption[
    Architecture logicielle du daemon d'interface avec le GPS]{
    Architecture logicielle du daemon d'interface avec le GPS}
    \label{fig:Architecture logicielle du daemon d'interface avec le GPS}
	\end{figure}

\vspace{1cm}

Le daemon \codeinline{text}{/usr/bin/mtk3339d} est invoqué et tué par son script d'initialisation\\\codeinline{text}{/etc/init.d/mtk3339d}.

\vspace{1cm}

Lors de son fonctionnement, il réceptionne les trames envoyées par le GPS sur la liaison série et en extrait les données intéressantes qu'il stocke dans sa mémoire. Ces données sont la latitude, la longitude, l'altitude, ainsi que le nom et la version du firmware, utilisés principalement comme débug.

La communication de ces données au logiciel principal du télescope se fait à la demande de ce dernier et par le biais d'un pipe FIFO pour chaque donnée.

\vspace{1cm}

Pour adresser sa requête des données au daemon (matérialisée par l'envoi d'un signal \codeinline{text}{SIGUSR1}), le logiciel principal a besoin de connaître le \codeinline{text}{PID} du daemon. Celui-ci est stocké dans le fichier \codeinline{text}{/var/run/mtk3339d.pid} créé par le script d'initialisation lors de l'invocation du daemon.

\vspace{1cm}

La fonction \codeinline{text}{init_gps} envoie la trame de configuration \codeinline{text}{PMTK314} décrite précédemment ainsi qu'une trame de requête des informations firmware \codeinline{text}{PMTK605}.

%\vspace{1cm}
\newpage

À l'usage, le daemon se lance automatiquement à l'allumage du système. On peut alors utiliser un programme de test \codeinline{text}{mtk3339d-test} contenant le fragment décrit ci-dessus du programme principal du télescope. Le test n'a pas eu l'occasion d'être fait dans un environnement où le GPS parvient à se connecter aux satellites, d'où les données nulles~:

\code{text}
root@autoscope ~ #
    mtk3339d-test
        GPS daemon PID : 335
        Recieved latitude : 0
        Recieved longitude : 0
        Recieved altitude : 0
        Recieved firmware : AXN_2.31_3339_13101700
\end{minted}

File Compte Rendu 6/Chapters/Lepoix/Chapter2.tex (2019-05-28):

\chapter{Hardware}

%TODO choix composants (IMU, GPS)? position carte?

\section{Architecture}

\begin{figure}[H]
    \centering
    
    \decoRule
    \caption[
    Schéma structurel de premier niveau du télescope]{
    Schéma structurel de premier niveau du télescope}
    \label{fig:Schéma structurel de premier niveau du télescope}
    \end{figure}

\vspace{1cm}

La première question de l'étude structurelle du télescope est celle de l'alimentation.

Le télescope sera raccordé au secteur par un module externe $220VAC / 12VDC$. Ensuite les moteurs seront alimentés en $12V$ via leurs contrôleurs respectifs et la Raspberry-Pi sera alimentée en 5V. Un convertisseur $12V / 5V$ est donc a ajouter.

Le télescope est également doté d'un ventilateur situé sous le miroir primaire et servant à le maintenir à température constante. Celui-ci sera alimenté en $12V$.

\vspace{1cm}

Tous les autres éléments seront alimentés en $3,3V$ par la Raspberry-Pi. Il est toutefois important de s'assurer que la consommation maximale en courant de ces élément ne dépasse pas ce que peut fournir la Raspberry-Pi, à savoir $500mA$.
\begin{itemize}[label=$\bullet$]
	\item Contrôleurs des moteurs ($\times 3$)~: $8mA$
	\item GPS~: $25mA$
	\item IMU~: $3,7mA$
	\item Capteurs de position des moteurs ($\times 5$)~: $33\mu A$
	\end{itemize}

\vspace{1cm}

La consommation en courant totale des périphériques de la Raspberry-Pi est largement inférieure à $500mA$, le montage est donc réalisable sans risque de dysfonctionnement ou de dommages.

\section{Conception du circuit}

\begin{figure}[H]
    \centering
    
    \decoRule
    \caption[
    Schéma structurel de la carte du télescope]{
    Schéma structurel de la carte du télescope}
    \label{fig:Schéma structurel de la carte du télescope}
    \end{figure}

\vspace{1cm}

Ce schéma ne présente pas de subtilité particulière, la plupart des composants étant des connecteurs.

\vspace{1cm}

L'alimentation est composée de~:
\begin{itemize}[label=$\bullet$]
	\item Un interrupteur d'allumage
	\item Une diode polarisante
	\item Une diode zener (TVS) protégeant des surtensions
	\item Un fusible protégeant des surintensités
	\item Un convertisseur DC/DC intégré
	\end{itemize}

\vspace{1cm}

L'environnement des boutons poussoirs servant de capteurs de butée aux mouvements du télescope est le suivant~:

\begin{figure}[H]
    \centering
    
    \decoRule
    \caption[
    Schéma de l'environnement des capteurs de butée]{
    Schéma de l'environnement des capteurs de butée}
    \label{fig:Schéma de l'environnement des capteurs de butée}
    \end{figure}

\vspace{1cm}

La valeur élevée des résistances de pullup $100k\Omega$ a pour but de réduire au maximum le courant consommé lors de l'appui, à $33\mu A$. Le courant prélevé par l'entrée GPIO de la Raspberry-Pi est de l'ordre de $0,5\mu A$.

Les condensateurs de $100nF$ permettent de filtrer les parasites générés par les rebonds propres aux boutons ainsi que les perturbations électromagnétiques.

\section{Contraintes de design}

\subsection{Contraintes électromagnétiques}

La première contrainte vient de la proximité du système électronique de deux moteurs, ceux-ci générant d'importantes perturbations électromagnétiques. Cela peut être particulièrement dérangeant pour le fonctionnement de la centrale inertielle et du GPS.

La solution la plus simple et efficace est de déporter ces deux modules le long de la structure du télescope.

%\vspace{1cm}

\subsection{Contraintes mécaniques}

Ensuite viennent les contraintes mécaniques de l'association de la carte à la Raspberry-Pi.

\vspace{1cm}

Tout d'abord, l'emplacement du connecteur et des fixations sont à prendre en compte.
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

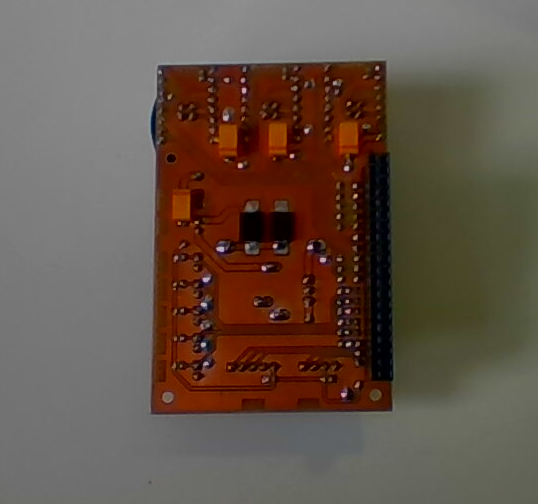
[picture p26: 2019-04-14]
Compte Rendu 6/Figures/photo_hardware3.png

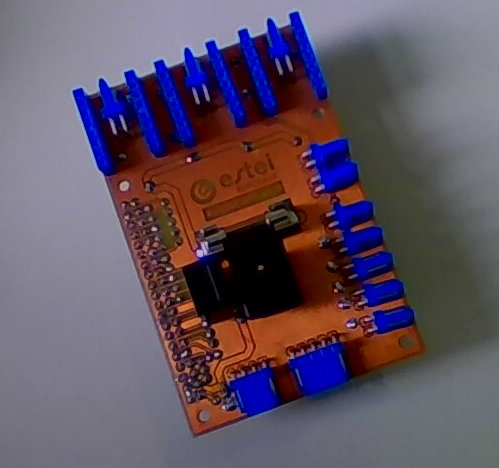
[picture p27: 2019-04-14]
Compte Rendu 6/Figures/photo_hardware1.png

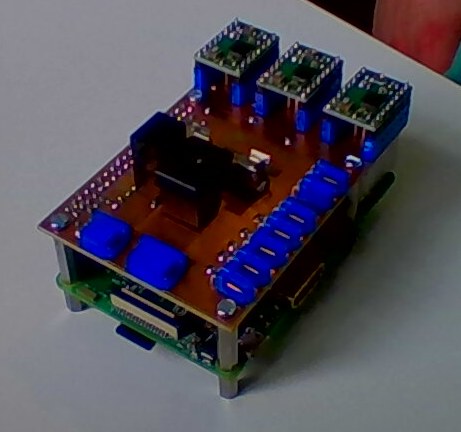
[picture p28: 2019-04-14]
Compte Rendu 6/Figures/photo_hardware2.png

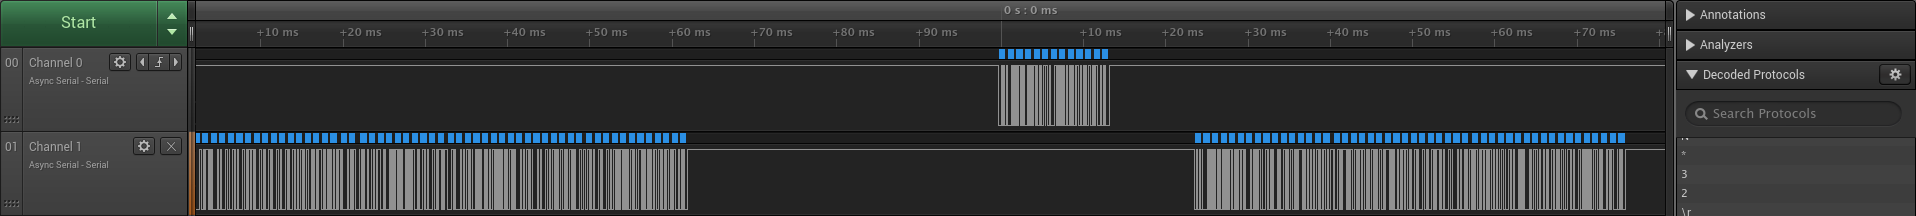
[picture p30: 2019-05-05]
Compte Rendu 6/Figures/osc_uart2.png

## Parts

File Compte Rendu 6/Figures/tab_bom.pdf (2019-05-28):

Référence | Valeur | Nom du produit | Nom du fabricant | Référence du fabricant | Nom du fournisseur Référence du fournisseur Quantité Prix unitaire HT (€) Prix TTC (€) Total (€)
Optique | -254mm ; F/D=5 Miroir parabolique Optique Unterlinden KE031 1 325 325 -70mm Miroir plan Optique Unterlinden KE035 1 70 70
| -7mm –21mm Occulaire Omegon Astro-shop 5084 1 59 59
454
Mécatronique | - | Moteur pas à pas | 17HM15-0904S | Gotronic | 31119 | 2 | 17,42 | 20,9 | 41,8
| - | Moteur pas à pas | S20TH30-0604A | Gotronic | 31107 | 1 | 19,08 | 22,9 | 22,9
| | | | | | | | | 64,7
SOC | -Raspberry Pi 3 B Raspberry Pi RASPBERRYPI3-MODB-1GB Farnell 2525225 1 29,29 29,29 -8Mp Raspi Camera v2 Raspberry Pi RPI 8MP CAMERA BOARD Farnell 2510728 1 22,19 22,19 -16GB Carte micro SD Sandisk SDSDQAB-016G Mouser 467-SDSDQAB-016G 1 9,8 9,8
| -1,20m ? Nappe CSI 1 0
61,28
- | Contrôleur moteur | Pololu | Pololu | 1182 | 3 | 5,23806 | 15,71418
- | 1,575GHz | Module GPS | Adafruit | Ultimate-GPS-746 | Mouser | 485-746 | 1 | 34,89 | 34,89
- | | Module IMU | Sparkfun | SEN-13762 | Mouser | 474-SEN-13762 | 1 | 13,06 | 13,06
U1 | | Module DC/DC | Recom | R-78B5.0-2.0 | Mouser | 919-R-78B5.0-2.0 | 1 | 8,62 | 8,62
- | | Alimentation AC/DC | XP Power | VEC65US12 | Farnell | 2524410 | 1 | 21,75 | 21,75
- | | Connecteur alim | CUI inc | PP-013 | Mouser | 490-PP-13 | 1 | 0,987 | 0,987
J6 | | Connecteur alim | CUI inc | PJ-043H | Mouser | 490-PJ-043H | 1 | 0,707 | 0,707
| | Header | Amphenol | 76383-302LF | Mouser | 649-76383-302LF | 3 | 0,987 | 2,961
- | | Header | Amphenol | 65239-002LF | Mouser | 649-65239-002LF | 3 | 0,341 | 1,023
| | Header | Amphenol | 76382-302LF | Mouser | 649-76382-302LF | 7 | 0,498 | 3,486
- | | Header | Amphenol | 65240-002LF | Mouser | 649-65240-002LF | 7 | 0,201 | 1,407
J7 | | Header | Amphenol | 76382-304LF | Mouser | 649-76382-304LF | 1 | 0,699 | 0,699
- | | Header | Amphenol | 65240-004LF | Mouser | 649-65240-004LF | 1 | 0,314 | 0,314
J9 | | Header | Amphenol | 76382-305LF | Mouser | 649-76382-305LF | 1 | 0,882 | 0,882
- | | Header | Amphenol | 65240-005LF | Mouser | 649-65240-005LF | 1 | 0,402 | 0,402
- | 2,54mm | Contacts Header | Amphenol | 76357-401LF | Mouser | 649-76357-401LF | 36 | 0,192 | 6,912
J8 | | Header | Samtec | ESQ-120-33-T-D | Mouser | 200-ESQ12033TD | 1 | 4,54 | 4,54
[U2 ; U4] | | Header | Amphenol | 76341-308LF | Mouser | 649-76341-308LF | 6 | 0,996 | 5,976
D2 | | Diode TVS | Littlefuse | SMCJ12A | Mouser | 576-SMCJ12A | 1 | 0,54 | 0,54
D1 | | Diode Schottky | MMC | SK54L-TP | Mouser | 833-SK54L-TP | 1 | 0,445 | 0,445
| | Condensateur | Kemet | T491X107K016AT | Mouser | 80-T491X107K016 | 3 | 1,96 | 5,88
| | Condensateur | Yageo | CC0805KRX7R9BB104 | Mouser | 603-CC805KRX7R9BB104 | 11 | 0,131 | 1,441
| | Résistance | Bourns | CR0805-FX-1003ELF | Mouser | 652-CR0805FX-1003ELF | 5 | 0,087 | 0,435
- | OFF-(ON) | Bouton poussoir | Omron | SS-5GL111 | Mouser | 653-SS-5GL111 | 5 | 1,98 | 9,9
-OFF-ON Interrupteur 0
-19mm ; M2,5 ; FF Entretoise RAF M1266-2545-SS Mouser 761-M1266-2545-SS 4 1,62 6,48 -10mm ; M2,5 ; MF Entretoise RAF M2105-2545-SS Mouser 761-M2105-2545-SS 4 1,37 5,48 -6mm ; M2,5 Vis Keystone 29301 Mouser 534-29301 4 0,361 1,444

-?mm ; M2,5 Vis 0
F1 5×20mm ; 6,3A Porte fusible Bulgin FX0321 Mouser 422-FX0321 1 1,62 1,62 -5×20mm ; 3A Fusible Bel Fuse 5MF 3 -R Mouser 530-5MF3-R 3 0,175 0,525

-12V Ventilateur 0
158,52018
Total (€) 738,50018

0,9° ; 5,4V ; 0,9A
1,8° ; 3,9V ; 0,6A

Carte
Électronique

12V ; 5V ; 2A
12V ; 5,41A
M ; 4mm ; 1,7mm
F ; 4mm ; 1,65mm
[J10 ; J12] | 2×2 ; M ; 90° ; 2,54mm
| 2×2 ; F ; Wire ; 2,54mm
SW1 ; [J1 ; J5] ; J13 | 1×2 ; M ; 90° ; 2,54mm
| 1×2 ; F ; Wire ; 2,54mm
| 1×4 ; M ; 90° ; 2,54mm
| 1×4 ; F ; Wire ; 2,54mm
| 1×5 ; M ; 90° ; 2,54mm
| 1×5 ; F ; Wire ; 2,54mm
| 2×20 ; F ; 2,54mm ; 16,13mm
| 1×8 ; F ; 2,54mm
| 14V ; DO-214AB
| 5A ; DO-214AB
[C9 ; C11] ; C15 | 100µF ; 16V ; C2917
[C1 ; C8] ; [C12 ; C14] | 100nF ; C0805
[R1 ; R5] | 100kΩ ; R0805

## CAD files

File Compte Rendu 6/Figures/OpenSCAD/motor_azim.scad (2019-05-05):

//color("yellow")
//bottom circle
    rotate_extrude($fn=100)
        translate([20, 0])
        square([10, 4]);
//belt
color("grey")
    rotate_extrude($fn=100)
        translate([19, 0])
        square([1, 4]);
//belt notches
color("grey")
    for(i=[0:10:360])
        rotate(i)
        translate([18, 0])
        cube([1, 1, 4]);
//sensor trigger
color("grey")
    translate([0, 30, 2])
    rotate([90, 0, 180])
    cylinder(4, 0.5, 0.5, $fn=100);


//top circle
    rotate_extrude($fn=100)
        translate([20, 30])
        square([10, 4]);
//motor
color("grey")
    translate([-4, 12, 30])
    cube(8);
//motor axis
color("grey")
    translate([0, 16, 24])
    cylinder(6, 0.5, 0.5, $fn=100);
//motor wheel
color("grey")
    translate([0, 16, 24])
    cylinder(2, 3, 3, $fn=100);
//sensor
color("grey")
    translate([-4, 30, 30])
    cube([8, 2, 3]);
color("grey")
    translate([-3, 30, 30])
    rotate([0, 30, 0])
    cube([6, 2, 0.2]);
color("grey")
    translate([-3, 30, 30])
    rotate([0, 30, 0])
    translate([6, 0, 0])
    rotate([0, -60, 0])
    cube([2, 2, 0.2]);

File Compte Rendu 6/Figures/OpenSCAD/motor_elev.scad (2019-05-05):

//color("yellow")
//bottom circle
/*    rotate_extrude($fn=100)
        translate([20, 0])
        square([10, 4]);
//belt
color("grey")
    rotate_extrude($fn=100)
        translate([19, 0])
        square([1, 4]);
//belt notches
color("grey")
    for(i=[0:10:360])
        rotate(i)
        translate([18, 0])
        cube([1, 1, 4]);
//sensor trigger
color("grey")
    translate([0, 30, 2])
    rotate([90, 0, 180])
    cylinder(4, 0.5, 0.5, $fn=100);
*/

//top circle
    rotate_extrude($fn=100)
        translate([20, 30])
        square([10, 4]);
//motor
color("grey")
    translate([-4, 12, 30])
    cube(8);
//motor axis
color("grey")
    translate([0, 16, 24])
    cylinder(6, 0.5, 0.5, $fn=100);
//motor wheel
color("grey")
    translate([0, 16, 24])
    cylinder(2, 3, 3, $fn=100);
//sensor
color("grey")
    translate([-4, 30, 30])
    cube([8, 2, 3]);
color("grey")
    translate([-3, 30, 30])
    rotate([0, 30, 0])
    cube([6, 2, 0.2]);
color("grey")
    translate([-3, 30, 30])
    rotate([0, 30, 0])
    translate([6, 0, 0])
    rotate([0, -60, 0])
    cube([2, 2, 0.2]);


//supports
	rotate([0, 0, 90])
	translate([9, 18, 34])
	cube([11, 4, 8]);
	rotate([0, 0, 270])
	translate([9, 18, 34])
	cube([11, 4, 8]);
	rotate([0, 0, 90])
	translate([-9-11, 18, 34])
	cube([11, 4, 8]);
	rotate([0, 0, 270])
	translate([-9-11, 18, 34])
	cube([11, 4, 8]);
//bows
	rotate([0, 90, 0])
	translate([-66, 0, 19])
	difference() {
		cylinder(2, 30, 30, $fn=100);
		translate([-20, -10, -1])
		cylinder(4, 35, 35, $fn=100);
		}
	rotate([0, 90, 180])
	translate([-66, 0, 19])
	difference() {
		cylinder(2, 30, 30, $fn=100);
		translate([-20, 10, -1])
		cylinder(4, 35, 35, $fn=100);
		}
//motor
color("grey")
    translate([-4, 20, 34])
    cube(8);
color("grey")
    translate([4, 24, 38])
	rotate([0, 90, 0])
    cylinder(4, 0.5, 0.5, $fn=100);
color("grey")
    translate([8, 24, 38])
	rotate([0, 90, 0])
    cylinder(2, 3, 3, $fn=100);
//wheel
color("grey")
	rotate([0, 0, 180])
	translate([-19, 16, 38])
	rotate([0, 90, 0])
    cylinder(38, 0.5, 0.5, $fn=100);
color("grey")
    translate([8, -16, 38])
	rotate([0, 90, 0])
    cylinder(2, 3, 3, $fn=100);
//axis
color("grey")
	translate([-19, 26, 76])
	rotate([0, 90, 0])
    cylinder(38, 0.5, 0.5, $fn=100);
color("grey")
	rotate([0, 0, 180])
	translate([-19, 24, 52])
	rotate([0, 90, 0])
    cylinder(38, 0.5, 0.5, $fn=100);
//belt
color("grey")
	translate([8, -16, 35])
	cube([2, 40, 0.5]);
color("grey")
	translate([10, -19, 37.3])
	rotate([69, 0, 180])
	cube([2, 15.5, 0.5]);
color("grey")
	translate([8, 27, 37.3])
	rotate([90.7, 0, 0])
	cube([2, 39, 0.5]);
//sensor
color("grey")
    translate([-18, 14, 39])
    cube([2, 8, 3]);
color("grey")
    translate([-18, 21, 42])
    rotate([0, -30, -90])
    cube([8, 2, 0.2]);
//sensor
color("grey")
    translate([-18, -22, 39])
    cube([2, 8, 3]);
color("grey")
    translate([-16, -21, 42])
    rotate([0, -30, 90])
    cube([8, 2, 0.2]);

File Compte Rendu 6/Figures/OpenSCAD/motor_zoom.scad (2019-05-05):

	rotate_extrude($fn=8)
    translate([24, 0])
    square([5, 2]);
	rotate_extrude($fn=8)
    translate([24, 20])
    square([5, 2]);

	rotate([0, 0, 22.5])
	translate([22.5, -10])
	difference() {
		cube([4, 20, 20]);
		translate([-2, 10, 11])
		rotate([0, 90, 0])
		cylinder(10, 8, 8, $fn=100);
		}
	rotate([0, 0, 22.5+90])
	translate([22.5, -10])
	difference() {
		cube([4, 20, 20]);
		translate([-2, 10, 11])
		rotate([0, 90, 0])
		cylinder(10, 8, 8, $fn=100);
		}
	rotate([0, 0, 22.5+180])
	translate([22.5, -10])
	difference() {
		cube([4, 20, 20]);
		translate([-2, 10, 11])
		rotate([0, 90, 0])
		cylinder(10, 8, 8, $fn=100);
		}
	rotate([0, 0, 22.5+270])
	translate([22.5, -10])
	difference() {
		cube([4, 20, 20]);
		translate([-2, 10, 11])
		rotate([0, 90, 0])
		cylinder(10, 8, 8, $fn=100);
		}

	rotate([0, 0, 22.5])
	translate([23, -2])
	cube([55, 4, 2]);
	rotate([0, 0, 22.5])
	translate([22.5, -2, -3])
	cube([2.5, 4, 3]);
	rotate([0, 0, 22.5])
	translate([43, -4, -9])
	cube([10, 8, 19]);

//screw
color("grey")
	rotate([0, 0, 22.5])
	translate([23, 0, -1.5])
	rotate([0, 90, 0])
	cylinder(60, 0.5, 0.5, $fn=100);
color("grey")
	rotate([0, 0, 22.5])
	translate([23, 0, -1.5])
	rotate([0, 90, 0])
	linear_extrude(height = 60, center = false, convexity = 10, twist = -30000)
	translate([0.5, 0, 0])
	circle(r = 0.5, $fn=100);
color("grey")
	rotate([0, 0, 22.5])
	translate([23+60, 0, -1.5])
	rotate([0, 90, 0])
	cylinder(1, 2, 2, $fn=6);

//zoom
color("grey")
	rotate([0, 0, 22.5])
	translate([35, 0, 10])
	rotate([0, 90, 0])
	cylinder(20, 6, 6, $fn=100);
color("grey")
	rotate([0, 0, 22.5])
	translate([55, 0, 10])
	rotate([0, 90, 0])
	cylinder(10, 6, 6, $fn=10);
color("grey")
	rotate([0, 0, 22.5])
	translate([65, 0, 10])
	rotate([0, 90, 0])
	cylinder(10, 6, 6, $fn=100);

//motor
color("grey")
	rotate([0, 0, 22.5])
	translate([43, -2, -13])
	cube([10, 4, 4]);
color("grey")
	rotate([0, 0, 22.5])
	translate([50, 0, -11])
	rotate([0, 90, 0])
	cylinder(12, 0.5, 0.5, $fn=100);
color("grey")
	rotate([0, 0, 22.5])
	translate([60, 0, -11])
	rotate([0, 90, 0])
	cylinder(4, 7, 7, $fn=100);

//belt
color("grey")
	rotate([0, 0, 22.5])
	translate([60, -6.5, -11])
	rotate([87, 0, 0])
	cube([4, 23, 0.5]);
color("grey")
	rotate([0, 0, 22.5])
	translate([60, 7, -11])
	rotate([93, 0, 0])
	cube([4, 23, 0.5]);

//trigger
color("grey")
	rotate([0, 0, 22.5])
	translate([57, 0, 10])
	rotate([30, 0, 0])
	cylinder(20, 0.5, 0.5, $fn=100);
//sensor
color("grey")
	rotate([0, 0, 22.5])
	translate([49, -4, -3])
	rotate([0, 0, -90])
    cube([2, 8, 3]);
color("grey")
	rotate([0, 0, 22.5])
	translate([50, -6, 0])
	rotate([0, 0, -90])
    rotate([0, -30, 90])
    cube([8, 2, 0.2]);

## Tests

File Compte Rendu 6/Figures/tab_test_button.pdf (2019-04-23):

Button | Vin (V) | Vout (V) ↑ | Vout (V) ↓
Azimut 1 | 3,33 | 3,26 | 0,00
Elevation 2 | 3,33 | 3,26 | 0,00
Elevation 1 | 3,33 | 3,26 | 0,00
Zoom 2 | 3,33 | 3,26 | 0,00
Zoom 1 | 3,33 | 3,26 | 0,00

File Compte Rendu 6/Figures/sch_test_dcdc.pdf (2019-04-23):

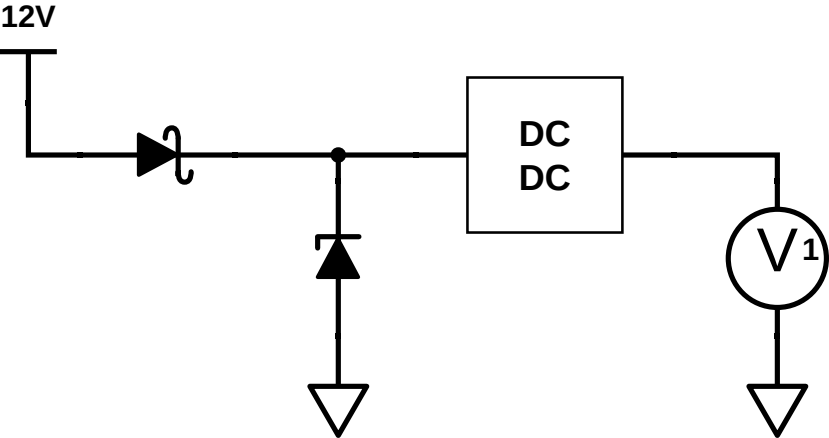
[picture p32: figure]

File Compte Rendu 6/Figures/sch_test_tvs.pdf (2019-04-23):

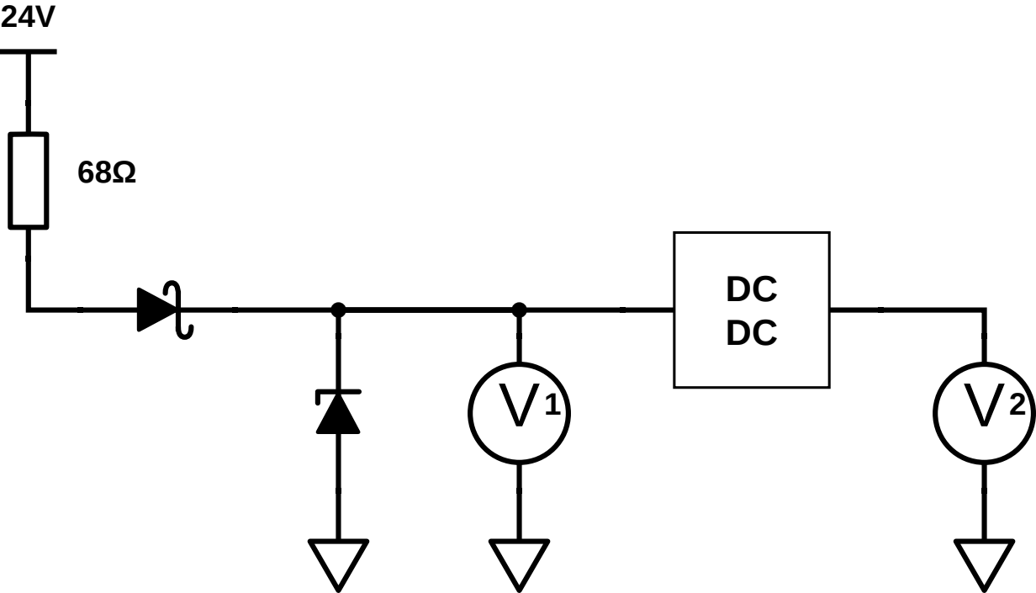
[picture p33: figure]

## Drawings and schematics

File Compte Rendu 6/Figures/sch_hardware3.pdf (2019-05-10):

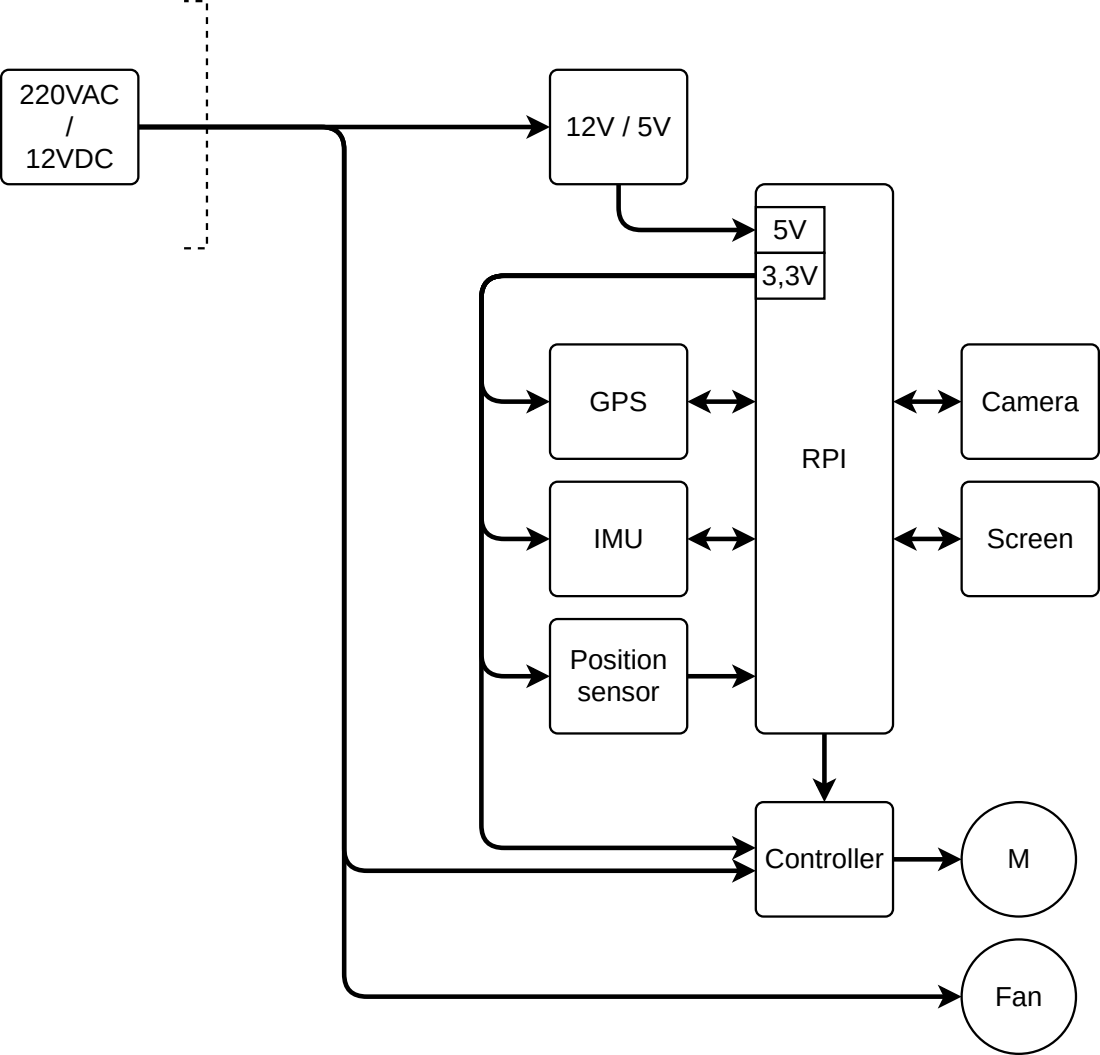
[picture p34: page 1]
GPS; IMU; Position sensor; Camera; Screen; RPI; 220VAC / 12VDC; Controller; Fan

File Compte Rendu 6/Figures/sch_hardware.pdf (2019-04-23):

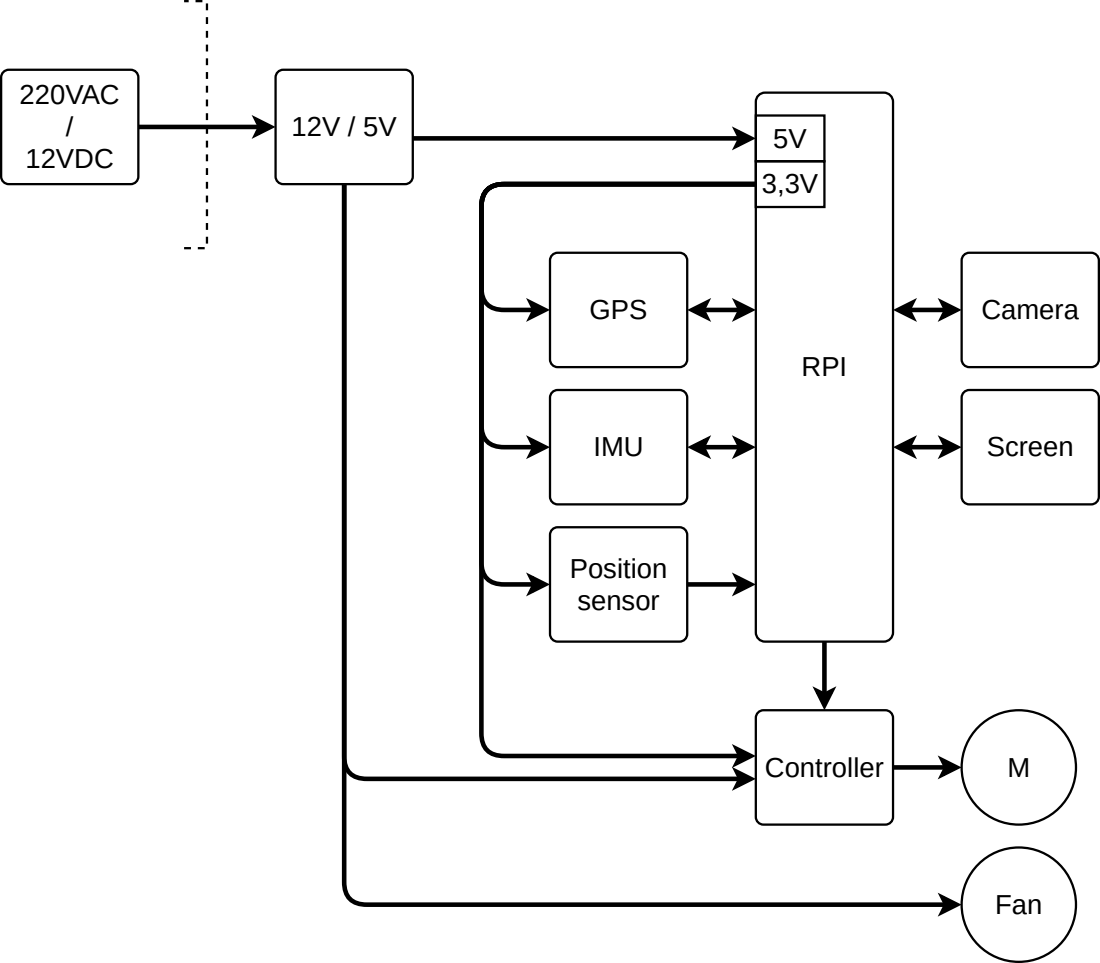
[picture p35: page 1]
GPS; IMU; Position sensor; Camera; Screen; RPI; 220VAC / 12VDC; Controller; Fan

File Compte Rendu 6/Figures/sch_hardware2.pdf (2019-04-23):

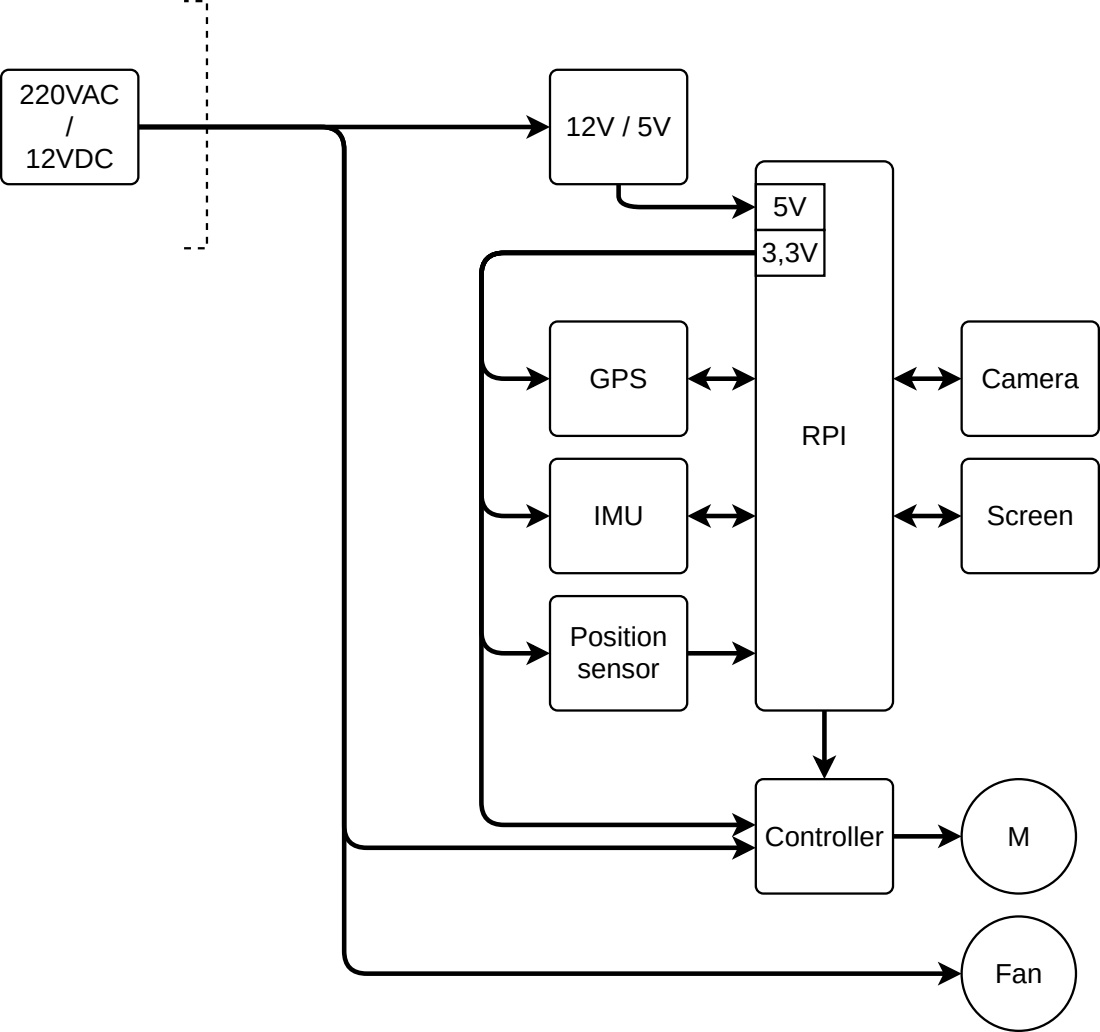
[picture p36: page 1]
GPS; IMU; Position sensor; Camera; Screen; RPI; 220VAC / 12VDC; Controller; Fan

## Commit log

2018-12-07 Add Compte_Rendu_1
    [tab_exigences.ods]
2019-01-07 move Figures
    [tab_exigences.ods]
2019-01-09 correction des fautes orthographe
2019-02-07 add autoscope 3
    [tab_imu.ods]
2019-03-26 add hello-mod probe messages
2019-04-23 add Compte rendu 6 LEPOIX
    [tab_test_button.ods]
2019-05-05 CR6 : update lepoix & begin CDC
    [motor_azim.scad, motor_elev.scad, motor_zoom.scad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]
